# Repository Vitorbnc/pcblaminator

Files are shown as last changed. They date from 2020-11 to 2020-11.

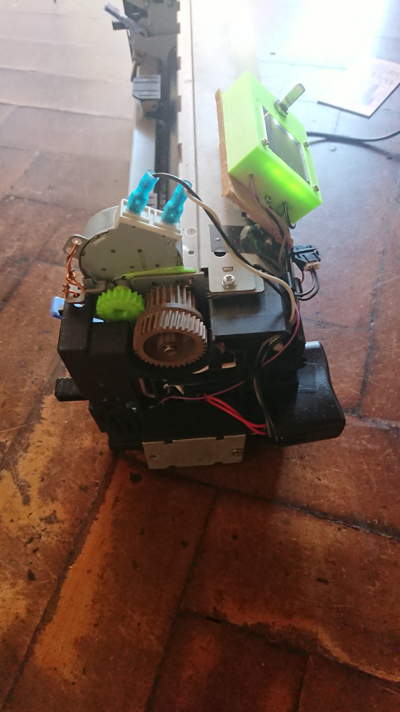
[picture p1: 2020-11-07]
view_side.JPG

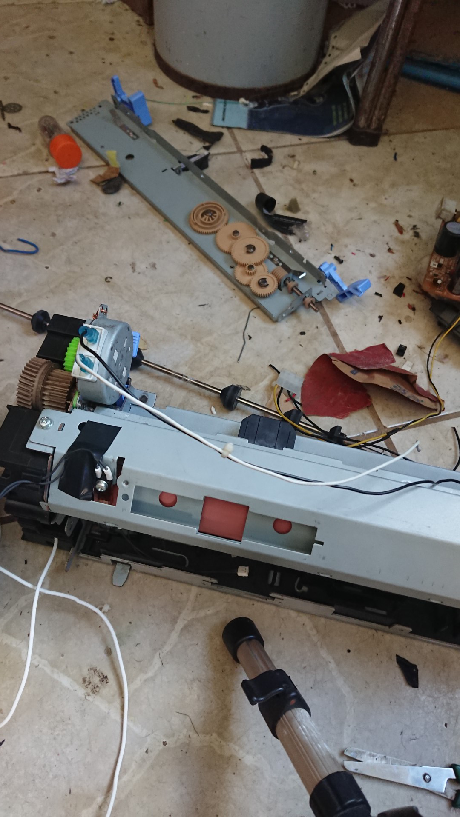
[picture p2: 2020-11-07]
view_top_no_mcu.JPG

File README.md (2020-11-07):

# pcblaminator
A Thermal Laminator for laminating PCBs and UV Photoresist made with an old  laserjet printer fuser

See a [quick demo (without photoresist)](https://youtu.be/e4A-39woypc).

Here you will find details on how to build a PCB laminator to use with uv-sensitive (dry-film, etc) methods. 

Inside the **src** folder there's code that runs in the STM32 MCU. The file **laminadora_ident_stm32** is the PID version and **laminadora_stm32** is the ON/OFF 
(aka bang-bang) control version.A system model was developed with matlab, although in the end I chose to keep the bang-bang version. 

The document **Relatório Laminadora** contains a detailed write-up of the procedures.The system model, PID implementation and write-up were carried on by us
as part of an assignment for our University Course.

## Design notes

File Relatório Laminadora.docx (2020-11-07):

UNIVERSIDADE FEDERAL DE LAVRAS DEPARTAMENTO DE ENGENHARIA - DEG LABORATÓRIO INTEGRADOR - GAT125

Professor: Daniel Furtado Leite

Modelagem e controle de temperatura de uma laminadora caseira

Bruna de Paula Faria - 201520782

Nicolas Iulius Lussari Brison - 201510916

Vitor Barbosa Nunes Costa - 201610290

6 de dezembro de 2019

Lavras – MG

Sumário

1. Introdução………………………………………………………………………………...….3

1.1 Objetivo.…………………………………………………………………………………….3

1.2 Fluxograma Geral………………………………………………………………………….3

1.3 Sobre Hardware, Software, Comunicação……………………………………………...4

2. Modelagem…………………………………………………………………………………..6

2.1 Calibração do sensor ....…………………………………....……...……………………..6

2.2 Aquisição de dados ……………………………………………………………………….8

2.3 Modelos Obtidos (Matlab/ident)…………………………………………………………..9

2.4 Simulações em Malha Aberta …………………………………………………………..12 3. Controle……………..………………………….………………………………………......13

3.1 Metodologia para Escolha de Parâmetros PID………………………………………..13

3.2 Projeto de Controle PID via Ziegler- Nichols……………………...……………..……14

3.3 Projeto de Controle PID via Cohen- Coon……………………………………………..15

3.4 Projeto de Controle PID via Cohen- Coon……………………………………………..17

3.5 Comparação da Malha Fechada em Simulação Matlab e Planta Física…………..18

4. Conclusão…………………………………………………………………………………..23

4.1. Síntese do Trabalho……………………………………………………………………..23

4.2. Dificuldades………………………………………………………………………………23

5. Referências………………………………………………………………………………....24

# 1. Introdução

Um grande desafio das pessoas que tem como hobbie a eletrônica ou prototipagem é a impressão de placas de circuito impresso. A dificuldade não se encontra na modelagem da placa, mas sim na impressão dos desenhos que devem ser transferidos para a placa, a fim de corroê-la de maneira correta. Antigamente, eram feitos desenhos à mão na placa, porém os resultados podiam ficar imprecisos muitas vezes.
Com a evolução e barateamento dos componentes e máquinas, hojé é possível fazer de forma mais fácil e eficiente a transferência do desenho para a placa: por meio de transferência térmica. Muitos amadores da eletrônicas utilizam ferros de passar roupa ou outras formas semelhantes para transferir a tinta do toner impresso no papel glossy, no entanto isso caracteriza muitas vezes um problemas, afinal a temperatura varia muito devido a ser um processo manual, aplicação de pressão variável no papel, dentre outras variáveis.

Uma solução muito viável para os hobbistas é utilizar uma laminadora, que é uma máquina com um sistema de dois cilindros rotativos, no qual um deles atinge a temperatura necessária para fundir o toner que foi despejado no papel glossy e transferi-lo para a placa de circuito impresso (PCI). Desta forma, se torna muito prática, rápida e barata a fabricação de PCI’s.

# 1.1. Objetivos

O objetivo deste trabalho é adquirir dados suficientes para obter um modelo matemático do sistema térmico, e utilizá-lo para controlar a temperatura da laminadora caseira, feita pelo grupo, testando e validando os modelos e o projeto do controlador.

1.2. Fluxograma Geral
Pode-se ver pela figura 1.1 a seguir o fluxograma geral do sistema. De maneira simplificada e visual ele mostra como os sinais são transmitidos dentro do sistema, apresenta também os principais elementos presentes nesta bancada.

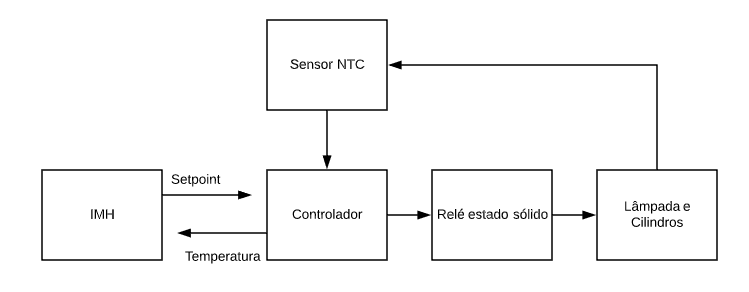
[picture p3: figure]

Figura 1.1 - Fluxograma Geral do Sistema

1.3. Sobre Hardware e Software

Os principais componentes da planta são:

• Par de cilindros

• Conjunto de lâmpadas para aquecimento

• Relé de estado sólido

• Microcontrolador STM-32

• Circuito eletrônico de condicionamento de sinal

• Sensor de temperatura

•Motor para rotação dos cilindros

• Fonte

• Tela para supervisão do usuário

• Encoder para definição do setpoint

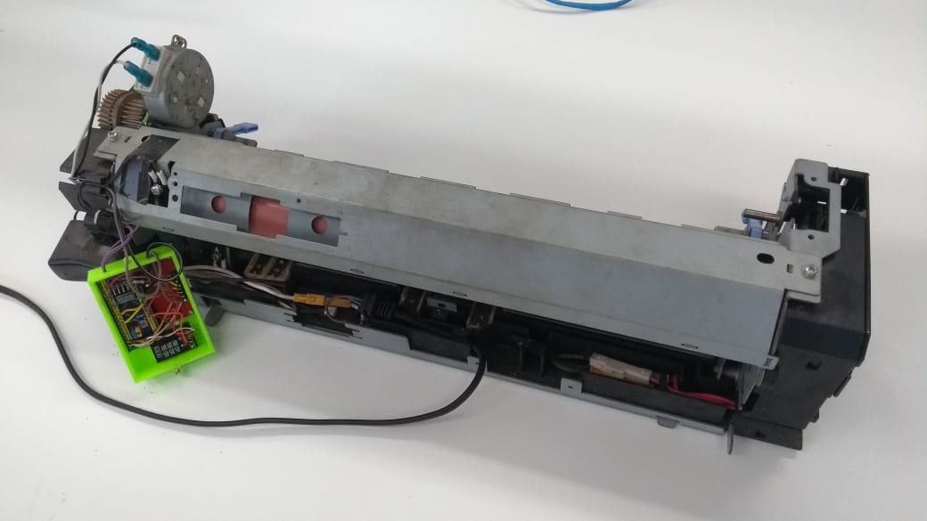
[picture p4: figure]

Figura 1.2 - Imagem real do sistema (frente)

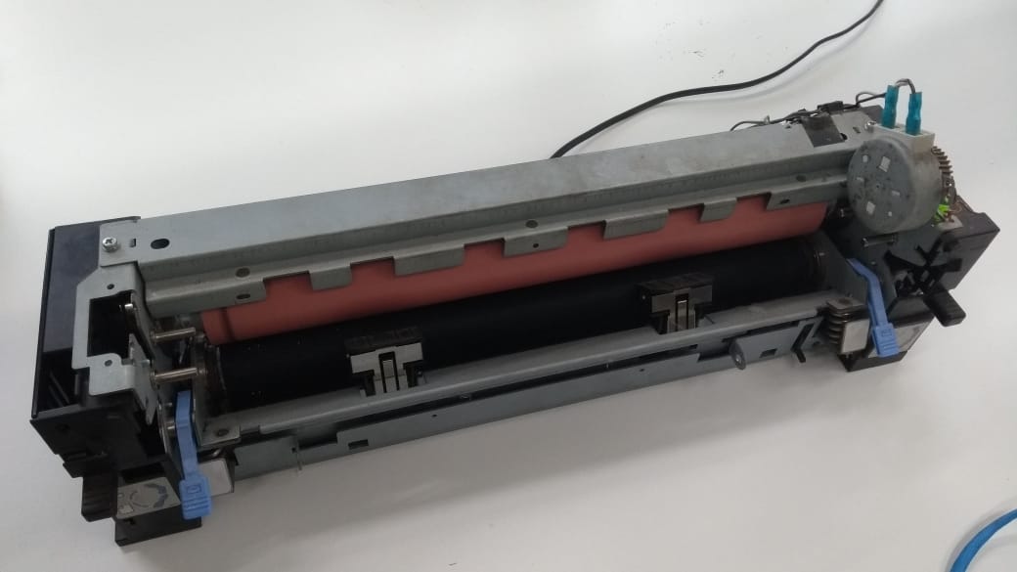
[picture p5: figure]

Figura 1.3 - Imagem real do sistema (verso)

O cilindro que esquenta a laminadora tem 3 lâmpadas em seu interior, e o controles será feito em cima destas lâmpadas. O distúrbio que o sistema sofre é quando a placa é inserida para que seja impresso o circuito, porém como a área da placa é muito pequena em relação a área dos cilindros, o distúrbio é irrelevante. O relé é utilizado para converter os sinais enviados pelo microcontrolador STM-32, para que a laminadoras seja alimentada com a tensão adequada. O microcontrolador faz a comunicação planta/ computador, ele faz a aquisição e controle dos sinais. A interface de comunicação entre computador e microcontrolador foi a ARDUINO IDE, na qual é permitida a comunicação com o STM-32.

A seguir, é apresentado o circuito elétrico da planta.

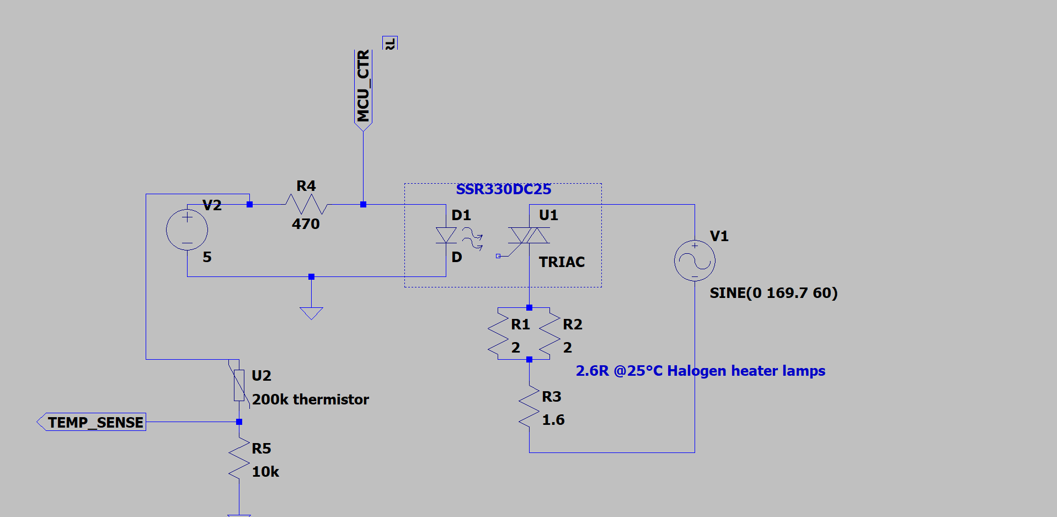
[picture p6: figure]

Figura 1.4 -Representação do circuito elétrico

No circuito podem ser notados o conjunto de lâmpadas, representados pelos resistores R1 a R3, o relé de estado sólido e o sensor de temperatura U2, que forma um divisor de tensão com o resistor R5.

2. Modelagem

2.1 Calibração do Sensor

Para fazer aquisição dos dados de temperatura, inicialmente era necessário conhecer a curva de calibração do sensor. Como não havia datasheet disponível, a curva de calibração foi determinada experimentalmente, e os resultados estão disponíveis no gráfico abaixo.

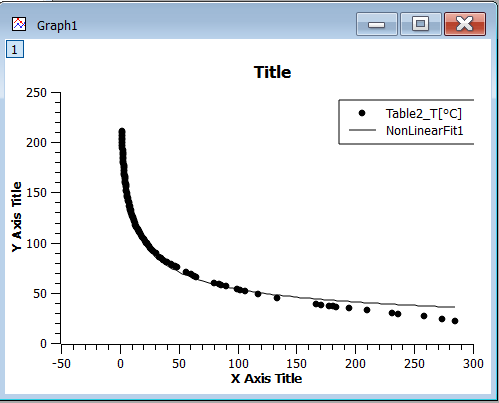
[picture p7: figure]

Figura 2.1 -Fit com a equação de Steinhart-Hart

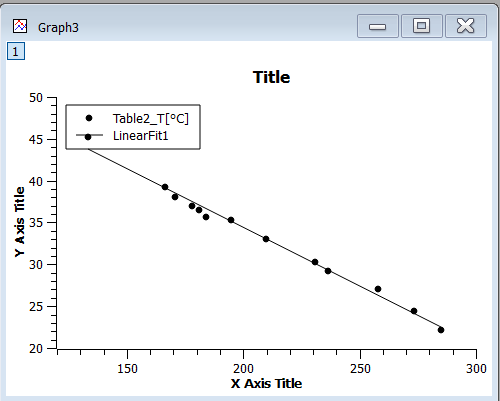
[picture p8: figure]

Figura 2.2 -Fit com a equação Linear

As duas equações foram utilizadas, sendo que o software do microcontrolador alterna entre elas de acordo com a faixa de temperatura, garantir que a saída do sensor se aproxima da real temperatura do sistema.

2.2. Aquisição dos dados

Para determinar o modelo da planta, foi dado um degrau de máximo de ciclo de trabalho na planta, e os dados foram coletados a cada 100 ms pelo cabo USB que conecta à porta serial, com auxílio de um adaptador USB-Serial RS232.

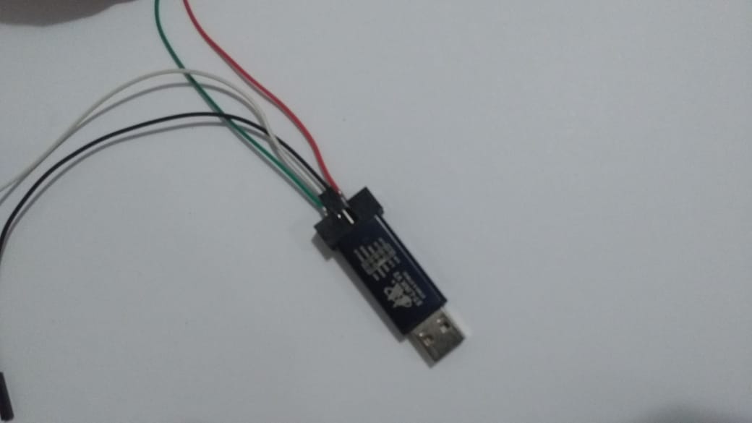
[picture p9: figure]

Figura 2.3 - Cabo para conexão

A partir dos dados, que foram coletados em formato .txt, foi possível trabalhar com eles no MatLab Ident.

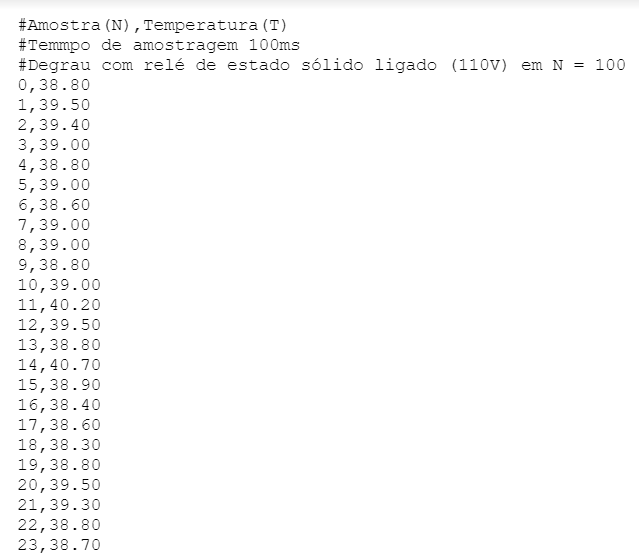
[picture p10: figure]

Figura 2.4 - Dados adquiridos

2.3. Modelos Obtidos (Matlab/Ident)

Foi levantado o modelo do sistema com a toolbox de identificação de sistemas do MatLab. Para poder realizar posteriormente o controle, um sistema de primeira ordem com tempo morto foi utilizado como modelo para o Ziegler Nichols e Cohen Coon, porém para o projeto com lugar das raízes foi escolhido um modelo de terceira ordem.

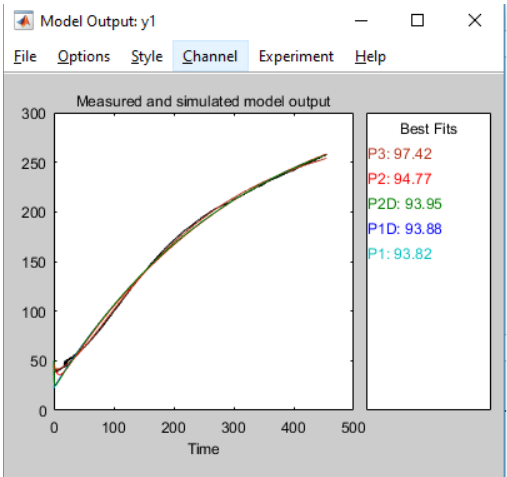
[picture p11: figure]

Figura 2.5 - Fits dos vários modelos levantados para o sistema

Como mostrado na figura acima, para o lugar das raízes foi utilizado o modelo P3 (terceira ordem) que teve fit de 97,42% e para o ZN e Cohen Coon o modelo P1D (primeira ordem), que teve fit de 93,88%.

Para fins de comparação, foram testados diversos algoritmos no MatLab.

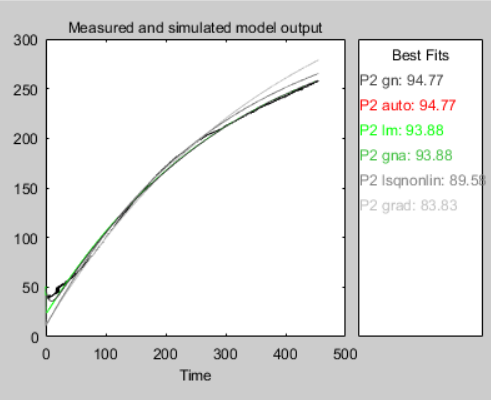
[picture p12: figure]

Figura 2.6 - Fits dos sistemas de segunda ordem

Os modelos acima se encaixam melhor dos que o de primeira ordem, porém como para o método Ziegler Nichols e Cohen Coon são utilizados modelo de primeira ordem, seria necessário aproximá-las, deixando o resultado parecido, logo optamos por usar as originais

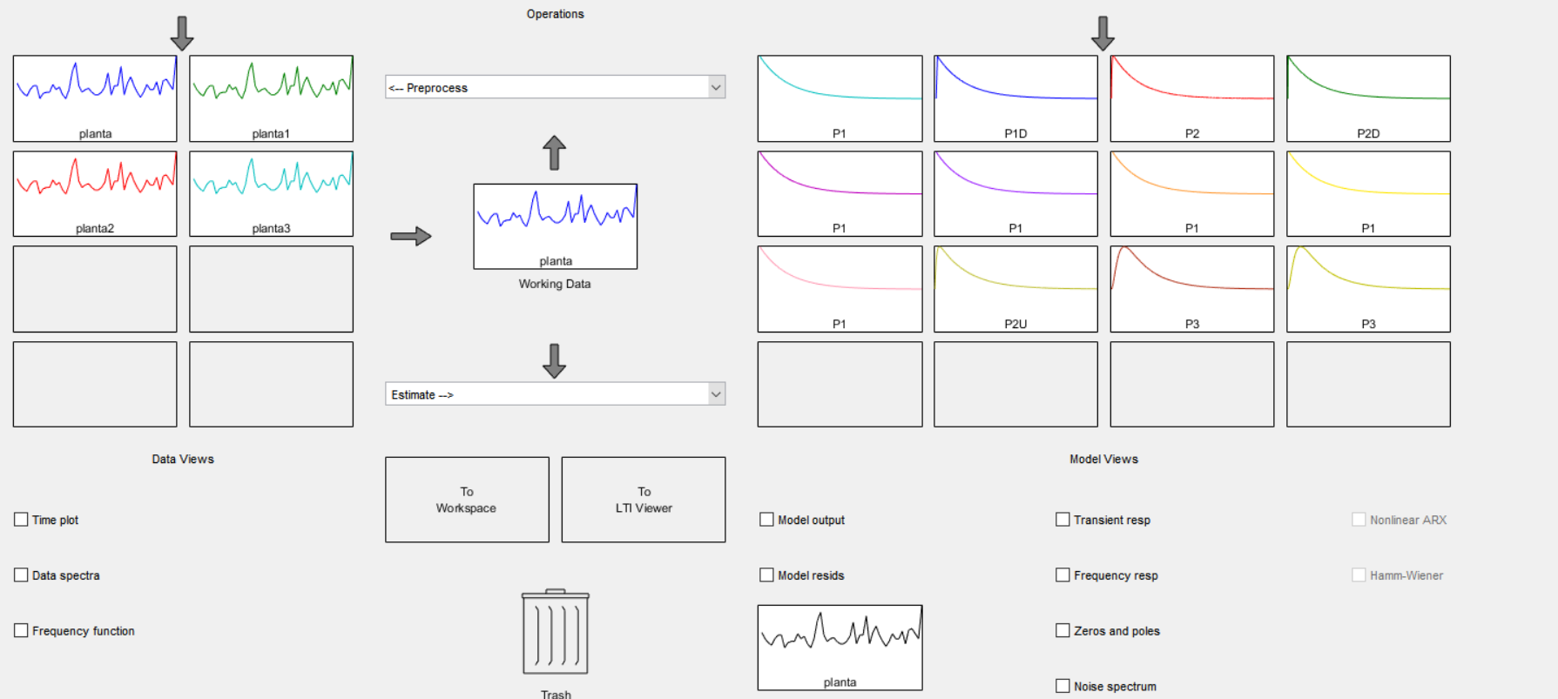
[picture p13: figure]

Figura 2.7 - Janela da Toolbox de Identificação de Sistemas

O modelo de primeira ordem adotado tem a forma da equação abaixo:

Figura 2.8 - Modelo de primeira ordem com atraso

O modelo de terceira ordem adotado tem a seguinte forma:

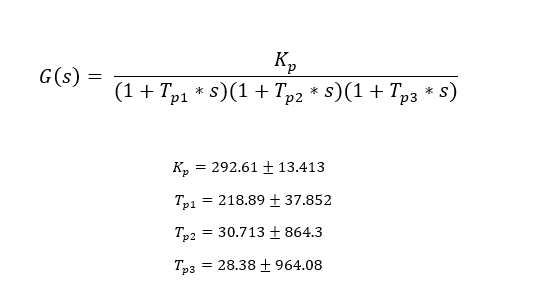
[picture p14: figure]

Figura 2.9 - Modelo de terceira ordem

Os algoritmos disponibilizados pelo MATLAB para ajuste de curvas também foram comparados. Para o modelo de segunda ordem, tanto o ajuste pelo Algoritmo de Levenberg-Marquardt quanto o algoritmo Gauss-Newton Adaptativo convergiram para os mesmos valores, e o algoritmo que melhor explicou os dados foi o algoritmo de Gauss Newton comum.

2.4. Simulações em Malha Aberta

Com os modelos determinados, procedeu-se à observação do comportamento do sistema em malha aberta. Os parâmetros foram inseridos no MatLab e a resposta ao degrau unitário foi simulada. Os resultados podem ser vistos nas duas figuras abaixo.

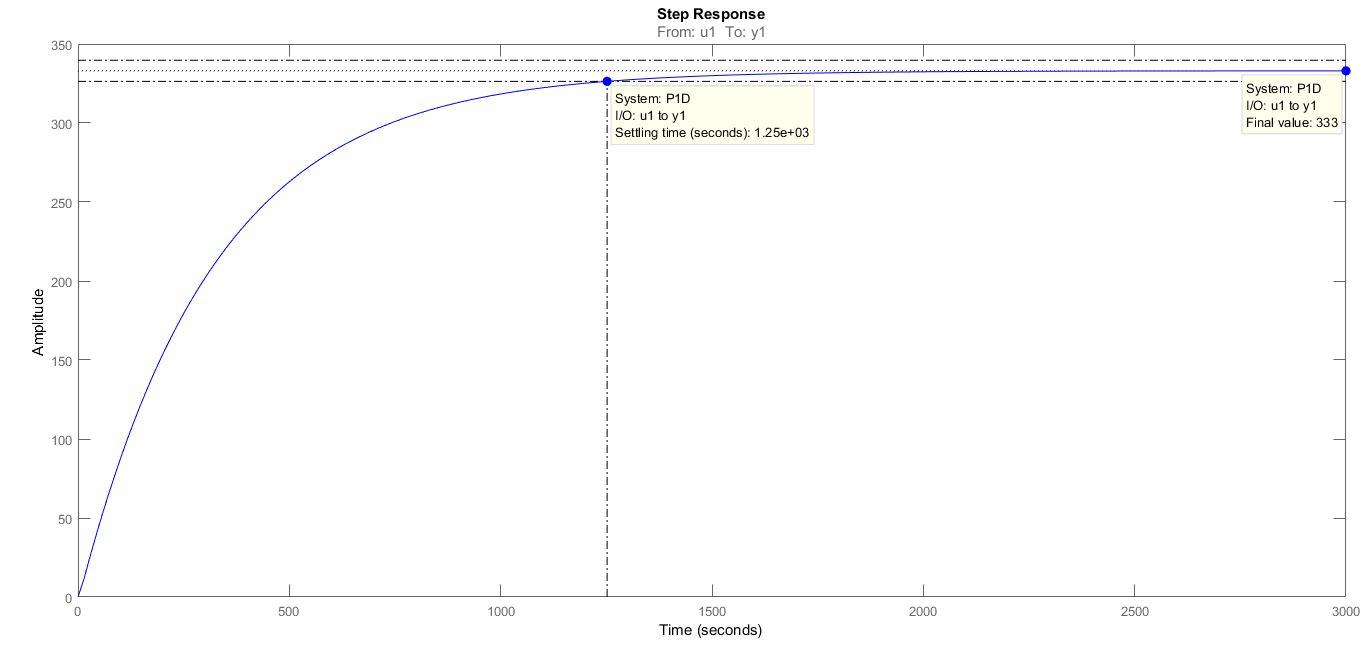
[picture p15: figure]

Figura 2.10 - Resposta ao degrau do modelo de primeira ordem com atraso

O modelo de primeira ordem apresentou tempo de assentamento de 1250 segundos, bastante longo, e um erro absoluto de 332 ao degrau unitário, valor também muito elevado.

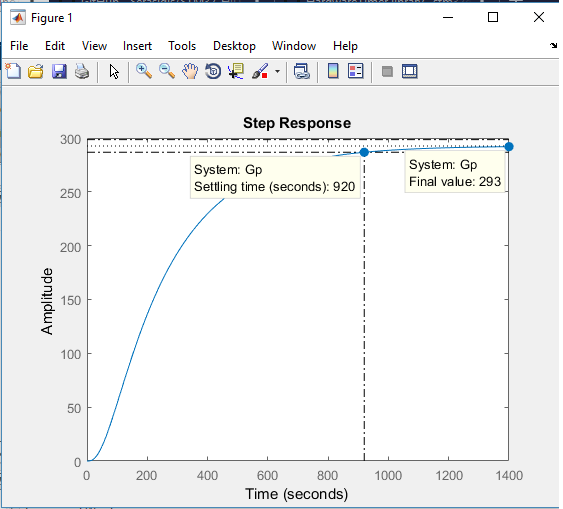
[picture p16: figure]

Figura 2.11 - Resposta ao degrau do modelo de terceira ordem com pólos reais

O modelo de terceira ordem será discutido melhor na próxima seção, dedicada ao Controle.

3. Controle

3.1 Metodologia para Escolha de Parâmetros PID

Repete-se aqui o gráfico de resposta ao degrau em malha aberta do modelo de terceira ordem, desta vez destacando as características relevantes para o projeto.

Figura 3.1 - Resposta ao degrau do modelo de terceira ordem

Como é possível notar no gráfico de resposta do degrau, o sistema apresentou erro absoluto em regime permanente de 292 e um tempo de assentamento bem longo de 920 segundos.

A partir destes dados, foi montado o projeto de um compensador capaz de zerar o erro ao degrau e melhorar o tempo de assentamento. Foi necessário um compensador PID, sendo que o integrador atuará para zerar o erro, enquanto o controle derivativo irá melhorar a resposta transiente, isto é, o longo assentamento do sistema.

3.2 Projeto de Controle PID via Ziegler-Nichols

Assim, o projeto do compensador PID foi feito utilizando o tradicional e testado método de Ziegler-Nichols para sintonia de controladores.

Inicialmente, a topologia foi definida e um diagrama de blocos para simulação do controle do sistema em malha fechada foi criado com auxílio do Simulink.

A partir das tabelas de Ziegler-Nichols para Sistemas Auto-Ajustáveis (que é o caso deste sistema, já que ele se estabiliza em um valor final determinado), da função de transferência de malha aberta e do gráfico de resposta ao degrau, definiram-se os ganhos adequados para o controlador.

Tabela 1 - Parâmetros do Controlador por Ziegler-Nichols para Sistemas Auto-Ajustáveis

Tabela 2 - Parâmetros do Controlador Determinados por Ziegler-Nichols

Kd | Kp | Ki | Td[s] = Kd/Kp | Ti[s] = Kp/Ki
191.52 | 127.68 | 21.28 | 1.5 | 6

3.3 Projeto de Controle PID via Cohen e Coon

Similarmente, foi projetado um controlador adicional através das técnicas de sintonia definidas por Cohen e Coon. O método é bastante parecido com Ziegler-Nichols, no sentido de que ambos utilizam uma aproximação de primeira ordem com atraso para o sistemas, no entanto, o procedimento de Cohen e Coon leva em conta o ganho estático do sistema.

Seguindo as tabelas de ajuste, analisando a resposta ao degrau em malha aberta e o modelo do sistema, os ganhos foram determinados.

Tabela 3 - Parâmetros do Controlador por Cohen e Coon para Sistemas Auto-Ajustáveis

Tabela 4 - Parâmetros do Controlador Determinados por Cohen e Coon

Kd | Kp | Ki | Td[s] = Kd/Kp | Ti[s] = Kp/Ki
0.1596 | 0.4321 | 0.0578 | 0.369 | 7.472

O código MATLAB usado para computar o modelo utilizado e os ganhos foi o seguinte:

s = tf('s')

%Modelo Ordem 1

K = 333.02;

tau = 319.21;

T = 3;

G1= K*exp(-T*s)/(1+tau*s)

figure(2)

step(G1)

%Ziegler-Nichols PID

Kp_zn = 1.2*tau/T

Ti_zn = 2*T

Td_zn = 0.5*T

Ki_zn = Kp_zn/Ti_zn

Kd_zn = Kp_zn*Td_zn

%Cohen-Coon PID

Kp_cc = tau/(K*T)*(1.35+0.27*T/tau)

Ti_cc = T*((2.5+0.5*T/tau)/(1+0.6*T/tau))

Td_cc = 0.37/(1+0.2*T/tau)

Ki_cc = Kp_cc/Ti_cc

Kd_cc = Kp_cc*Td_cc

%Controladores PID

%G_pid = Kd*s+ Kp +Ki/s

Gc_zn = Kp_zn + Ki_zn/s + Kd_zn*s

Gc_cc = Kp_cc + Ki_cc/s + Kd_cc*s

%Sistemas em malha fechada

T_zn = Gc_zn*G1

T_cc = Gc_cc*G1

T_zn = T_zn/(1+T_zn)

T_cc = T_cc/(1+T_cc)

%Degrau em malha fechada

figure(4)

subplot(1,2,1)

step(T_zn)

subplot(1,2,2)

step(T_cc)

3.4 Projeto de Controle PID via Lugar das Raízes

Para o modelo de terceira ordem, que melhor havia explicado os dados, procedeu-se com o projeto de um controlador pelo método de lugar das raízes.

Os parâmetros de projeto foram overshoot nulo ou de até 3% e tempo de assentamento próximo de 150s.

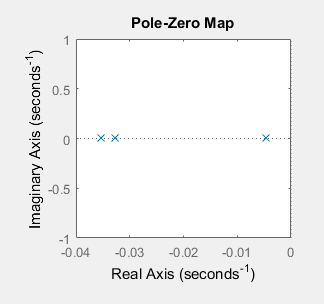
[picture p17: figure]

Figura 3.2 - Pólos do Sistema em Malha aberta

Para projetar o controlador, determinou-se que os pólos adicionais deveriam ser cancelados pelos zeros do compensador para manter a validade da aproximação de segunda ordem do sistema. O pólo intermediário foi mantido já que ele atendia de imediato as especificações de projeto, conforme a equação abaixo:

T_s =4/σ = 4/0.0326 = 122.7s

O ganho do compensador poderia ser determinado também pela condição de fase para os pólos de malha fechada desejados, mas optou-se por usar o gráfico de lugar das raízes do Matlab para determinar o maior ganho possível com mínimo de overshoot.

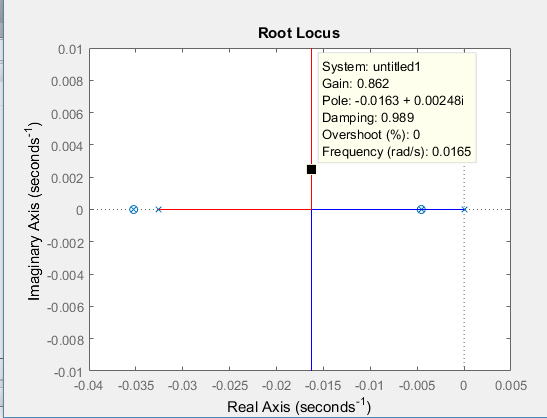
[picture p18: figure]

Figura 3.3 -Determinação dos Ganhos do Controlador

Tabela 5 - Parâmetros do Controlador por Lugar das Raízes

Kd | Kp | Ki | Td[s] = Kd/Kp | Ti[s] = Kp/Ki
0.205 | 0.0082 | 0.000033 | 25 | 248,48

3.5 Comparação da Malha Fechada em Simulação Matlab e Planta Física

Para verificar a validade parâmetros calculados, fez-se uma simulação no MATLAB do sistema em malha fechada com ambos os controladores, através do seguinte código:

%Controladores PID

%G_pid = Kd*s+ Kp +Ki/s

Gc_zn = Kp_zn + Ki_zn/s + Kd_zn*s

Gc_cc = Kp_cc + Ki_cc/s + Kd_cc*s

%Sistemas em malha fechada

T_zn = Gc_zn*G1

T_cc = Gc_cc*G1

T_zn = T_zn/(1+T_zn)

T_cc = T_cc/(1+T_cc)

%Degrau em malha fechada

figure(4)

subplot(1,2,1)

step(T_zn)

subplot(1,2,2)

step(T_cc)

O resultado pode ser visto no gráfico abaixo.

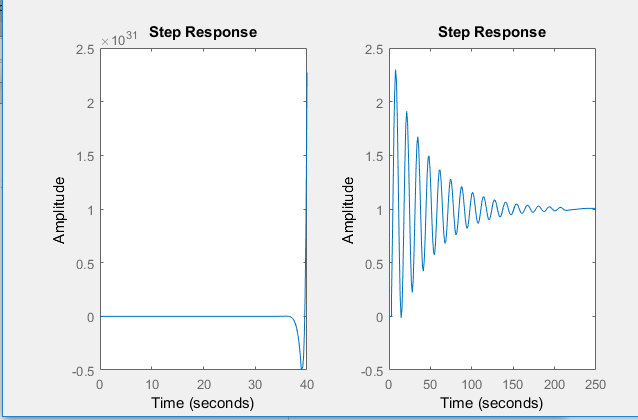
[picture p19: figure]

Figura 3.4 - Simulação para Ziegler-Nichols e Cohen e Coon, respectivamente

O resultado da simulação não foi satisfatório para as sintonias com modelo de primeira ordem com atraso. O controle com Ziegler-Nichols apresentou uma resposta ao degrau extremamente agressiva, e a saída foi a valores muito altos. O controle com Cohen-Coon atingiu o tempo de estabelecimento esperado e zerou o erro, mas com overshoot de mais de 100%.

Para o modelo de terceira ordem, o código de projeto e simulação utilizado no Matlab foi o seguinte:

s = tf('s');

%Modelo ordem 3

Gp = 292.61/((1+218.89*s)*(1+30.713*s)*(1+28.38*s))

subplot(2,2,1)

step(Gp)

Tplanta = feedback(Gp,1)

subplot(2,2,3)

step(Tplanta)

%Controlador PID

%Métricas desejadas, especificações realistas

%Eliminar erro em regime permanente-> PI

%Ts aprox = 150s, máx atingível para 100 graus com atuador saturado -> PID

%Max overshoot = 1%, o controle ON/OFF tem cerca de 11%

%PID raiz por lugar das raízes:

% zeros-> no polos de malha aberta

%Ts = 4/sigma -> sigma = 4/Ts

%Um dos pólos fica em zero (integrador)

%Segundo polo, parte real em 2*sigma, para que o root locus fique na metade

plant_poles = pole(Gp)

pzmap(Gp)

Gc = (s-plant_poles(1))*(s-plant_poles(3))/s

rlocus(Gp*Gc)

%Ganho escolhido pelo lugar das raízes, maior ganho com mínimo de overshoot (0.7%)

K = 0.205

Gc = K*Gc

T = feedback(Gp*Gc,1)

subplot(2,2,2)

step(T)

%Comparando coeficientes com PID canônico

%syms Kp Ki Kd S

%Gpid = Kp+Kd*S+Ki/S

%Gpid = (Kd*S^2+Kp*S+Ki)/S

Kd = 0.205;

Kp = 0.00816;

Ki = 3.3e-5;

O resultado da simulação pode ser visto na figura abaixo.

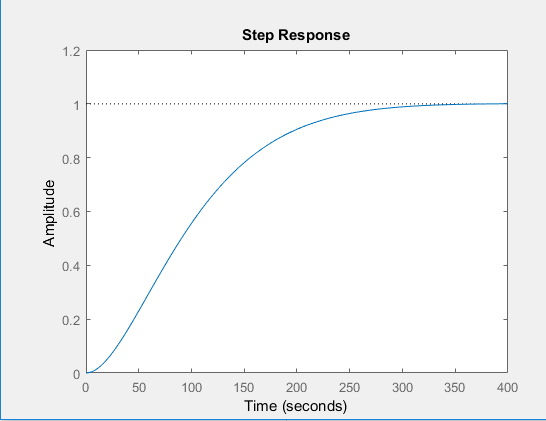
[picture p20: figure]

Figura 3.5 - Simulação para Lugar das Raízes

Para o controle projetado por lugar das raízes, a simulação foi muito satisfatória. Não houve qualquer ultrapassagem ou erro, e o tempo de estabelecimento foi dentro das especificações.

Após a simulação, o passo seguinte foi testar o controlador PID na planta, o que foi feito aplicando os ganhos calculados ao algoritmo de controle pela porta serial. Cada conjunto de ganhos foi aplicado uma vez para a aquisição dos dados, e então aguardava-se o resfriamento do sistema até que o novo conjunto de ganhos pudesse ser testado. Os ganhos testados, que são os mesmos calculados anteriormente, estão dispostos na tabela abaixo.

Tabela 6 - Parâmetros Finais

Metodologia | Kd | Kp | Ki | Td[min] = Kd/Kp | Ti[min] = Kp/Ki
Cohen e Coon | 0.1596 | 0.4321 | 0.0578 | 0.369 | 7.472
Ziegler e Nichols | 191.52 | 127.68 | 21.28 | 1.5 | 6
Lugar das Raízes | 0.205 | 0.0082 | 0.000033 | 25 | 248,48

Na figura seguinte, é apresentado a resposta da planta com o método root-locus, onde se obteve um overshoot de 38%, o que mostrou não ser o método mais adequado para o controle. O tempo de assentamento foi muito longo, portanto foi outro motivo para que não fosse utilizado esse modelo.

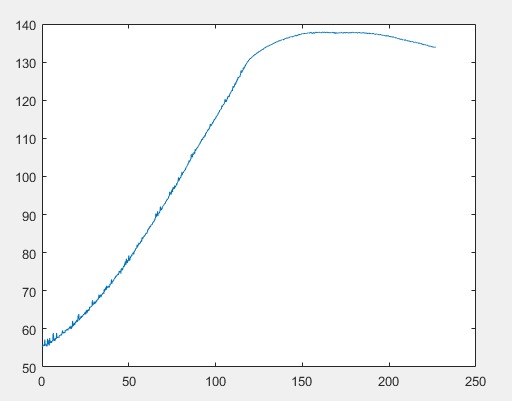
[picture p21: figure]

Figura 3.6 - Teste na planta com Root-locus, setpoint=100ºC

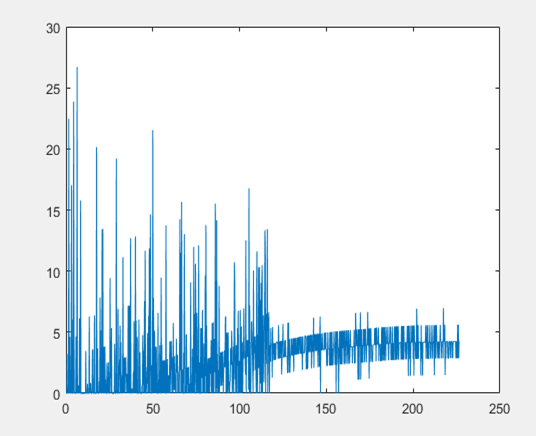
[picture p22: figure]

Figura 3.7 - Sinal de controle do controlador com Root-locus, setpoint=100ºC

Já neste caso abaixo, obteve-se pelo método de Cohen Coon, um overshoot menor, na faixa de 25%, o que ainda não é um resultado satisfatório. O tempo de assentamento apesar de menor, ainda não foi satisfatório.

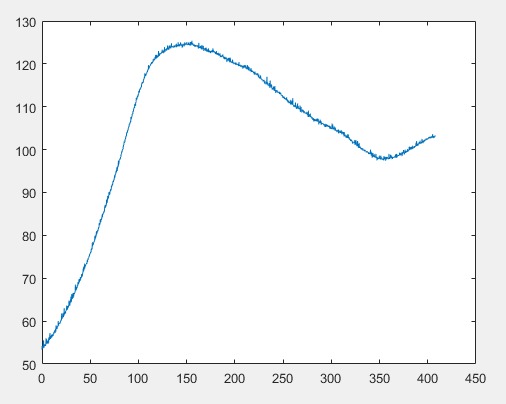
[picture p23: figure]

Figura 3.8 - Teste na planta com Cohen e Coon, setpoint=100ºC

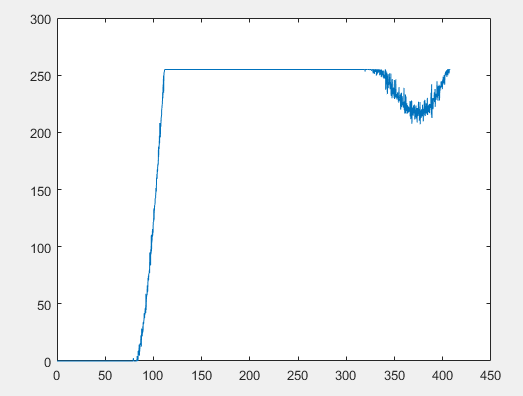
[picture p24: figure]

Figura 3.9 - Sinal de controle do controlador com Cohen-Coon, setpoint=100ºC

Finalmente, para o método de Ziegler-Nichols, obteve-se um overshoot bom, no valor de 10%, o qual definiu-se como a melhor situação para a planta. Também é possível observar que o tempo de assentamento de 250 segundos.

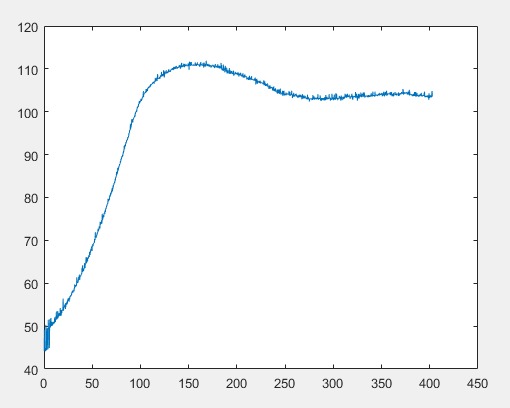
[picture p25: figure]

Figura 3.10 - Fim do teste na planta com Ziegler- Nichols, setpoint=105ºC

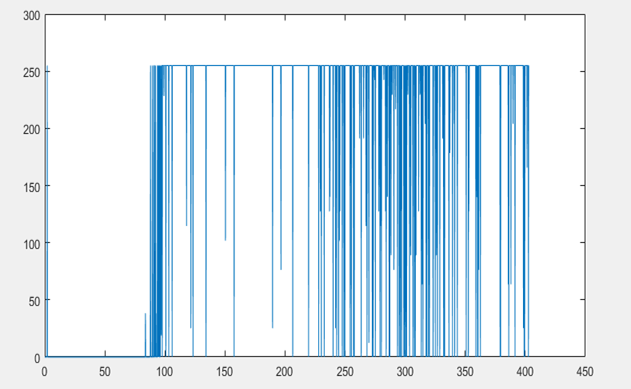
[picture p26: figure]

Figura 3.11 - Sinal de controle do controlador com Ziegler-Nichols, setpoint=105ºC

Os resultados da implementação foram inesperados. O controlador Ziegler-Nichols foi o que apresentou ação de controle mais agressiva dentre os dois, o sinal de saída do compensador oscilou bastante, mas o tempo de estabelecimento foi menor e houve ultrapassagem de cerca de 10%, dentro do esperado.

Com o controlador Cohen e Coon o sistema chegou a atingir o valor final após a ultrapassagem, mas depois o erro aumentou novamente.

O controlador do lugar das raízes foi o mais passivo dentre todos, e acabou levando a um overshoot muito grande, sem corrigi-lo com eficácia, acabando por não zerar o erro em regime permanente.

4. Conclusão

4.1. Síntese do Trabalho

O trabalho propôs-se a coletar dados para levantar um modelo teórico da planta de uma laminadora, que pode ser caracterizada como um sistema térmico, e portanto utilizar o modelo para projetar um compensador que seria aplicado na planta real para controle de temperatura.

Os modelos criados a partir das manipulações e utilização das ferramentas do MatLab apresentaram um alto grau de compatibilidade com os dados experimentais, com qualidade de ajuste (fit) de pelo menos 92%.

Embora a simulação dos modelos tenha sido satisfatória, o comportamento no sistema real se deu um pouco pior do que as simulações executadas, porém o overshoot, tempo de assentamento e erro permanente se apresentaram com bons valores, sendo assim um bom resultado para o projeto.

4.2. Dificuldades

Foram encontradas dificuldades para a concepção e montagem do projeto, e principalmente para encontrar os materiais necessários.

Além disso, também houve dificuldades para fazer o teste na planta, uma vez que era bem demorado o resfriamento da laminadora, e portanto, era gasto certo tempo para que novos testes fossem performados.

Nos códigos também houveram empecilhos, pois para a implementação foi necessário algum tempo de pesquisa e aprendizado.

5. Referências

Laminadora para placa de circuito impresso -Disponível em < http://www.luccas.com.br/index.php/eletronica/montagens/ 8-laminadora-para-placa-de-circuito-impresso>

Laminador de PCI feito com sucata - Disponível em < https://www.py2bbs.qsl. br/laminador.php (https://www.py2bbs.qsl.br/laminador.php) >

# Tutorial: Estimating a transfer function model from random input using MATLAB - Disponível em < https://www.youtube.com/watch?v=gFZNNe1qsR8 >

NISE, Norman S. Control Systems Engineering. Edição 6

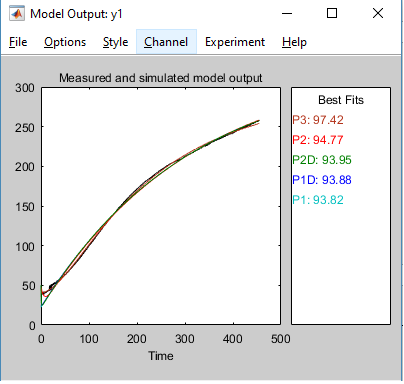
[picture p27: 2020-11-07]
system model and pid params/fits todos modelos novo.png

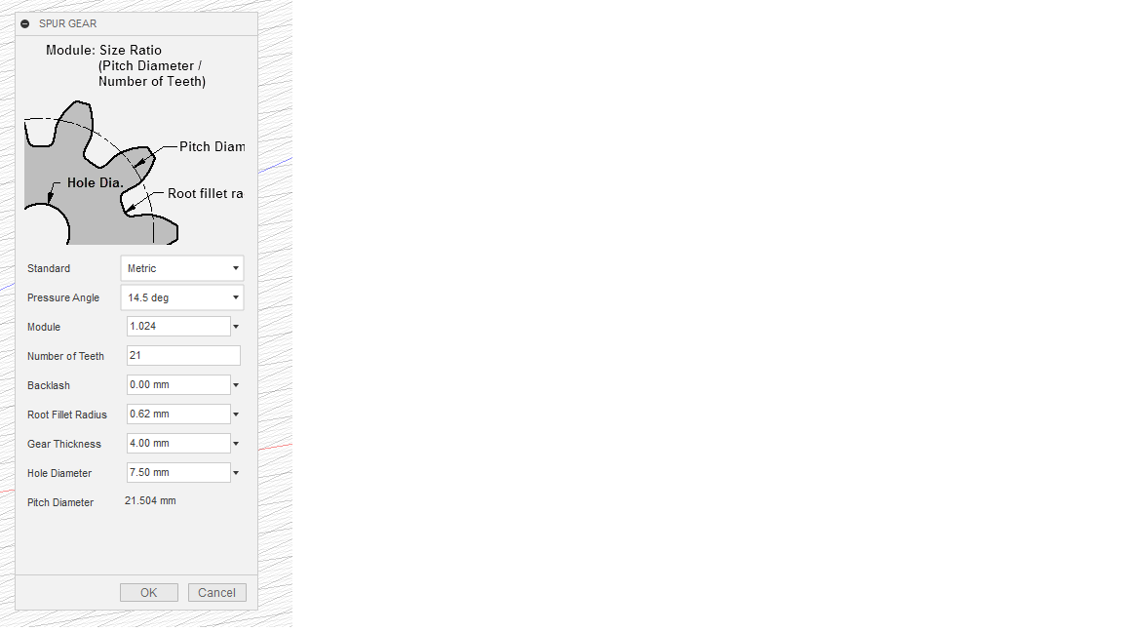
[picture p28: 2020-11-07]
Peças 3D/Fusion 360 RS6-0845 gear generator parameters.png

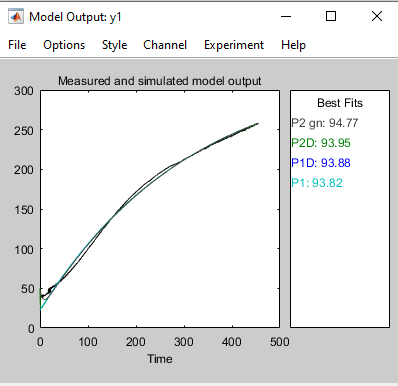
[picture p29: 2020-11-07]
system model and pid params/fits todos modelos.png

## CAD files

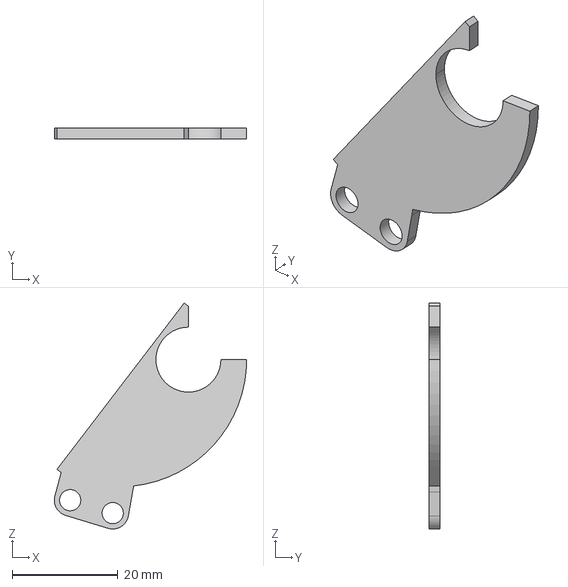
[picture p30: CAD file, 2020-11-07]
Peças 3D/microwave motor spacer and adapter v1.step
36.3 x 2.00 x 42.7 mm

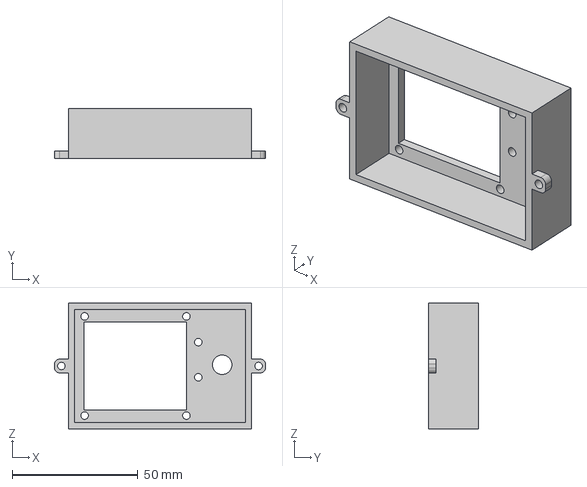
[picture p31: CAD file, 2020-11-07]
Peças 3D/Suporte LCD Nokia 5110 e Botao de Encoder v3.step
84.0 x 20.0 x 50.0 mm

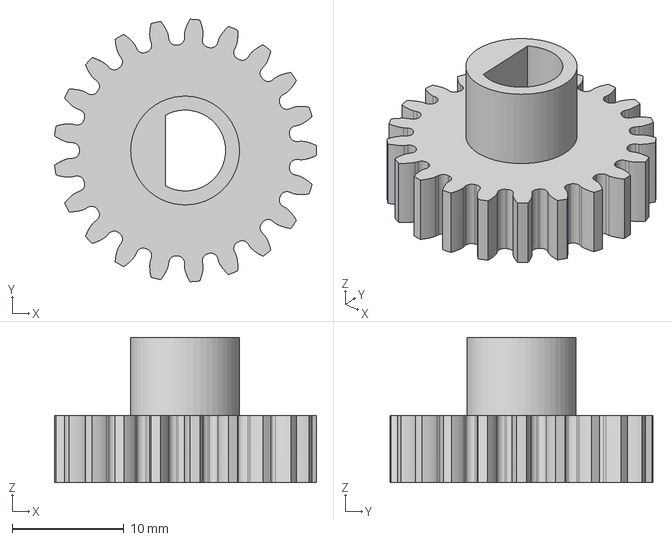
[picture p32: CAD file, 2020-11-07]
Peças 3D/RS6-0845 Gear 21 Teeth HP9000 Laser Fusor v3.step
23.5 x 23.5 x 13.0 mm

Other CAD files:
Peças 3D/RS6-0845 Gear 21 Teeth HP9000 Laser Fusor v3.f3d
Peças 3D/Suporte LCD Nokia 5110 e Botao de Encoder v3.f3d
Peças 3D/microwave motor spacer and adapter v1.f3d

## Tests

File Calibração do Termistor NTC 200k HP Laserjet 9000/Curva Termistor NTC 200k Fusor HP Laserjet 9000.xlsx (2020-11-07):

ADC | Tensão ADC [V] | R [kOhms] | T[°C] | ADC Bits | R1[Ohms] | Vin
3957 | 3.188 | 285.000 | 22.2 | 12 | 10000 | 3.3
3951 | 3.184 | 273.300 | 24.4 | 12 | 10000 | 3.3 | Legenda
3943 | 3.177 | 258.100 | 27 | 12 | 10000 | 3.3 |  | Alterável
3929 | 3.166 | 236.400 | 29.2 | 12 | 10000 | 3.3
3925 | 3.163 | 230.800 | 30.3 | 12 | 10000 | 3.3
3909 | 3.150 | 209.700 | 33 | 12 | 10000 | 3.3
3896 | 3.139 | 194.810 | 35.3 | 12 | 10000 | 3.3
3884 | 3.130 | 184.030 | 35.6 | 12 | 10000 | 3.3
3881 | 3.127 | 180.910 | 36.5 | 12 | 10000 | 3.3
3878 | 3.124 | 177.870 | 37 | 12 | 10000 | 3.3
3869 | 3.117 | 170.520 | 38 | 12 | 10000 | 3.3
3864 | 3.113 | 166.600 | 39.2 | 12 | 10000 | 3.3
3810 | 3.070 | 133.340 | 45.2 | 12 | 10000 | 3.3
3774 | 3.041 | 117.450 | 49.2 | 12 | 10000 | 3.3
3743 | 3.016 | 106.330 | 51.5 | 12 | 10000 | 3.3
3731 | 3.006 | 102.340 | 52.6 | 12 | 10000 | 3.3
3723 | 2.999 | 99.810 | 53.7 | 12 | 10000 | 3.3
3688 | 2.972 | 90.490 | 56.7 | 12 | 10000 | 3.3
3670 | 2.957 | 86.170 | 57.8 | 12 | 10000 | 3.3
3660 | 2.949 | 84.000 | 58.4 | 12 | 10000 | 3.3
3640 | 2.933 | 79.930 | 60.2 | 12 | 10000 | 3.3
3549 | 2.859 | 64.910 | 65.9 | 12 | 10000 | 3.3
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

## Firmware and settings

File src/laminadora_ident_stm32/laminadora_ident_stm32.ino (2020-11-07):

#include <Arduino.h>
#include "Nokia_5110.h"
#include <math.h>
#include<EEPROM.h>

#define LCD_BACKLIGHT PC13
#define BTN PA15

#define ENCODER_CLK PA11
#define ENCODER_DT PA12

#define THERMISTOR PA0
#define SS_RELAY PA2

#define ADC_BITS 12

bool serialEnabled = false;

#define SAMPLING_PERIOD 100

unsigned long lastSampleTime  = 0;

unsigned long currentSample = 0;


// Constants for Steinhart-Hart Equation, got from SciDaVis fit
const float STEIN_A = 0.00436953656192422;
const float STEIN_B = 0.000942199116744498;
const float STEIN_C = 0.000101710499635659;

const float LIN_B = 62.4688362492716;
const float LIN_A = -0.140370799828433;

const int THERMISTOR_DIVIDER_R1 = 10000;//9979; //Ohms 
const float THERMISTOR_DIVIDER_VIN = 3.28;


//Nokia_5110 lcd = Nokia_5110(RST, CE, DC, DIN, CLK);
Nokia_5110 lcd = Nokia_5110(PB3,PB5,PB4,PA7,PA5);


bool lastEncCLK = true;

int encoderPos = 0;

int setpoint = 0;
float currentTemp = 0;
const int tempThreshold = 1;
const int firstTempThreshold = 5;
bool firstHeating = true;

void encoderISR(){
  if(digitalRead(ENCODER_DT))
    encoderPos++;
  else
    encoderPos--;
}

int resistanceFromADC(int adc_val){
  float vout = THERMISTOR_DIVIDER_VIN/4095*adc_val;
  //return vout;
  return THERMISTOR_DIVIDER_R1/(THERMISTOR_DIVIDER_VIN/vout -1.0);
}
float temperatureFromResistance(float R){
  //return R;
  R = R/1000.0;
    if(R<125.0)
      return 1/(STEIN_A+STEIN_B*log(R)+STEIN_C*pow(log(R),3));
    else
      return LIN_A*R + LIN_B;
}

float readTemperature(){
  int mean = 0;
  for(int i=0;i<5;i++)
    mean+=analogRead(THERMISTOR);

  int temp = 10*temperatureFromResistance(resistanceFromADC(mean/5));
  currentTemp = temp/10.0;
  return currentTemp;
}

/*
uint16_t encoderState = 0;
void encoderFilter(){
  //https://www.best-microcontroller-projects.com/rotary-encoder.html#Digital_Debounce_Filter
  // Debounce filter that checks for a FALLING edge
  //Encoder must be 1 then stay 0 for 12 cycles, giving 1111 0000 0000 0000
  //Operation OR with 0xe000 keeps 16-bit variable 1s on leftmost positions: 0xe000 = 1110 0000 0000 0000
  encoderState = (encoderState<<1) | digitalRead(ENCODER_CLK) | 0xe00;
  if(encoderState == 0xf00){
    encoderState = 0x00;
    //Falling edge with DATA high means clockwise motion 
    if(digitalRead(ENCODER_DT))
        encoderPos++;
      else 
        encoderPos--;
  }
}
*/

void readEncoder(){
    bool clk = digitalRead(ENCODER_CLK);
  if(clk and !lastEncCLK){ //rising edge
    if(digitalRead(ENCODER_DT)) //if true, got CCW motion
      encoderPos--;
    else
      encoderPos++;
  }
      lastEncCLK = clk;
      if(encoderPos<0)
        encoderPos=0;
      if(encoderPos>250)
        encoderPos = 250;
}

void splashScreen(){
  lcd.setCursor(0,0);
  lcd.print("LAMINADORA");
  lcd.setCursor(20,2);
  lcd.print("BULLDOZER");
  lcd.setCursor(0,4);
  lcd.print("por Vitor");
  delay(3000);
  lcd.clear();
}

void setup() {
  Serial.begin(115200);
  Serial.print("Sampling every ");
  Serial.print(SAMPLING_PERIOD);
  Serial.println(" ms");
  Serial.println("Number , Temperature");
  
  
  analogReadResolution(ADC_BITS);  

  pinMode(LCD_BACKLIGHT, OUTPUT);

  pinMode(BTN, INPUT);
  pinMode(ENCODER_CLK,INPUT);
  pinMode(ENCODER_DT,INPUT);
  //attachInterrupt(ENCODER_CLK,encoderISR,FALLING);

  pinMode(THERMISTOR,INPUT_ANALOG);
  pinMode(SS_RELAY,OUTPUT);

  digitalWrite(LCD_BACKLIGHT,LOW);
  lcd.setContrast(50);
  splashScreen();
  lcd.setCursor(0,0);
  lcd.println("Atual:");
  lcd.println("Set:");
  lcd.println("Entrada:");
  digitalWrite(SS_RELAY,HIGH);
  //setpoint = readTemperature();
  encoderPos = EEPROM.read(0);
  setpoint = encoderPos;
  if(setpoint-readTemperature()<firstTempThreshold)
    firstHeating = false;
}



void loop() {
  readEncoder();
  if(!digitalRead(BTN)){
    setpoint = encoderPos;
    EEPROM.update(0,encoderPos);
  }

  lcd.setCursor(50,0);
  
  float temp = readTemperature();
  lcd.print(temp);
  if(temp<100) lcd.print("  ");
  lcd.setCursor(50,1);
  lcd.print(setpoint);
  lcd.print("   ");
  lcd.setCursor(50,2);
  lcd.print(encoderPos);
  lcd.print("   ");

if(Serial.available())
  if((char)Serial.read()=='s')
    serialEnabled = !serialEnabled;
    
  if(serialEnabled and millis()-lastSampleTime>=SAMPLING_PERIOD){
    Serial.print(currentSample);
    Serial.print(",");
    Serial.println(temp);
    lastSampleTime=millis();
    if(currentSample==100)
      digitalWrite(SS_RELAY,LOW);
    currentSample++;
    
  }
  
//  int error = setpoint-int(floorf(currentTemp));
//  if(firstHeating){
//  
//    if(error>firstTempThreshold)
//      digitalWrite(SS_RELAY,LOW);
//    else {
//      digitalWrite(SS_RELAY,HIGH);
//      firstHeating = false;
//      delay(5000);
//  
//    }
//  }
//  else if(error>tempThreshold)
//    digitalWrite(SS_RELAY,LOW);
//  else
//    digitalWrite(SS_RELAY,HIGH);    
}
